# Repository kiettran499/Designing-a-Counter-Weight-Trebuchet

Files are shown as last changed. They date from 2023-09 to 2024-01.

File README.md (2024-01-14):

# Designing-a-Counter-Weight-Trebuchet

<p align="center">
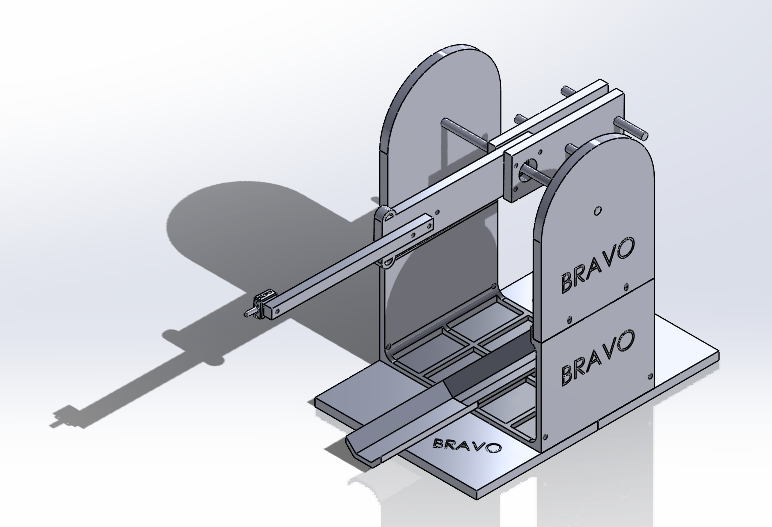
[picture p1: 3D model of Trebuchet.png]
  

## Description

- This project allows us to design and build the trebuchet which can throw the object like ping-pong ball over 5 meters using at least 2 500g PASCO weight.
- To design the trebuchet, there are several parameters might make a major contribution to the result and effectiveness of the trebuchet:
  - Mass Ratio between the Counterweight and the Projectile from law of conservation of energy.
  - Arm length ratio.
  - Friction in fulcrum.
- Some requirements:
  - The Trebuchet should not have more than 12 parts.
  - Each part should be able to fit into a 15 x 15 x 15 cm box.
  - The parts should have constant thicknesses of either 3 mm, 5 mm, or 10 mm and be made from Acrylic materials.
  - The Trebuchet shall permit aiming, which means it should be able to be adjusted for firing at different ranges and angles.

## Design & Result

- After doing calculations and simulate it in trebuchet virtual simulation, We came to the design.
<p align="center">
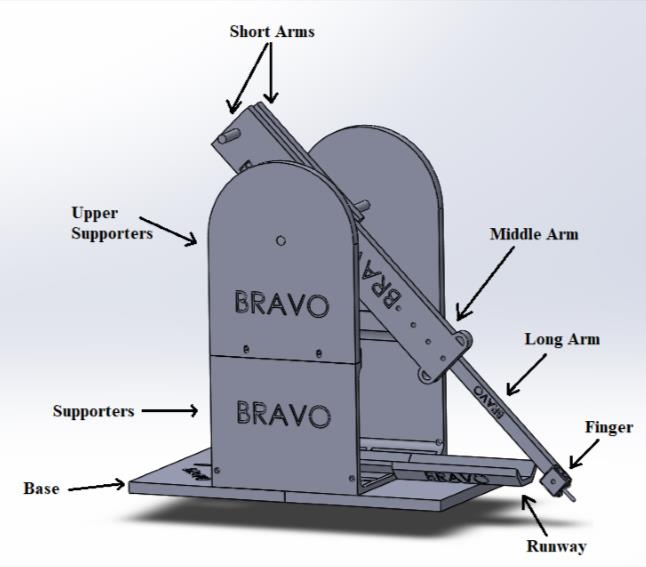
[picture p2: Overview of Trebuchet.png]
  
  
- Bill of Material.
<p align="center">
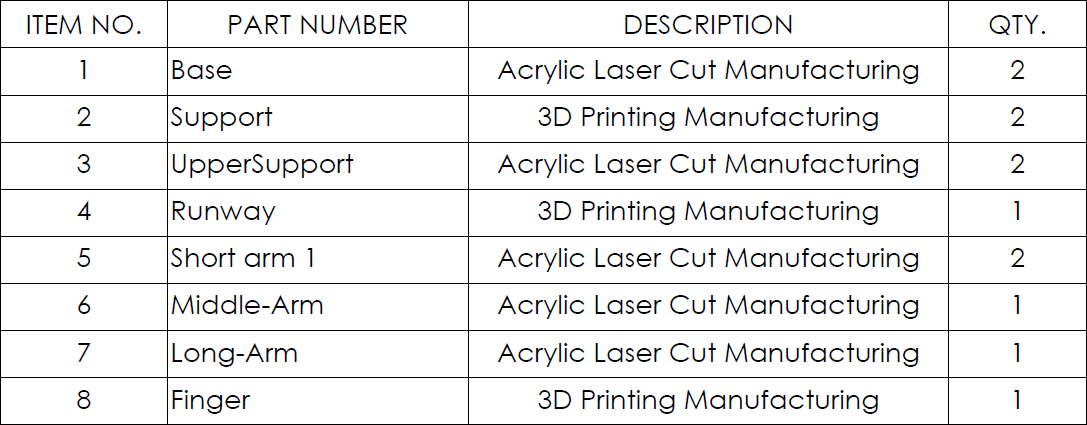
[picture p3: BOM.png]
  

- Exploded View of Trebuchet.
<p align="center">
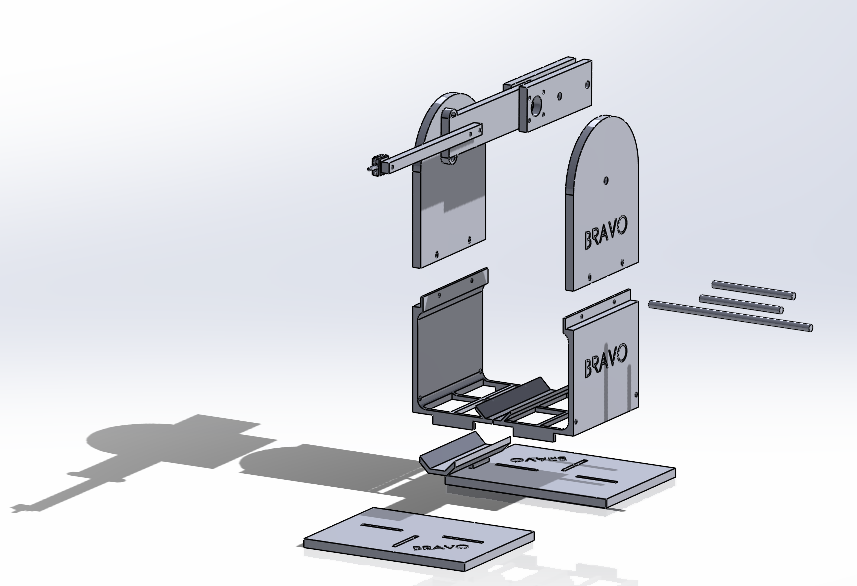
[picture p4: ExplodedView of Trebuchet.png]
  

- Exploded View of Trebuchet (Animation GIF).
<p align="center">
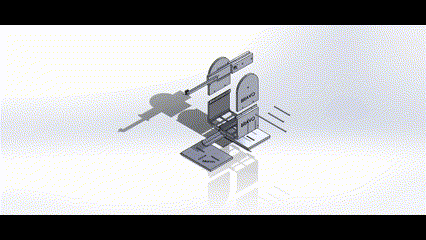
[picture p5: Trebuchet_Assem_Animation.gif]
  

- In conclusion, the trebuchet has 12 parts in total and each of them is fit into a 14 x 14 x 14 cm box. The projectile is the Ping-Pong ball and we choose 4 PASCO 500 grams weights whose total mass is 2000 grams.
- The length ratio between long and short arm is 4:1. The height of pivot is 23.5 cm as the height of each PASCO weight is 9cm and the short arm is 8cm, and we do not want them to hit the ground or the projectile runway when dropping. To leverage the arm ratio even more, we choose the sling whose length is close to that of the long arm, 30cm.
- Result: in the demonstration evaluation section, we had
  - 3 shots to test distance and all 3 shots are over 5 meters.
  - 1 shot to test accuracy and we had successfully hit the target at 4 meters.

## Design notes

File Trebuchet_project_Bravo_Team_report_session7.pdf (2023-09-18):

OENG1505 – Creative Engineering CAD | Page 1 of 21

# Class Project Designing a Counterweight Trebuchet

Student Numbers | Student Names:
s3758994 s3752562 s3741189 s3754450 s3757327 s3750474 | Nguyen Quoc Minh Truong Minh Phu Tran Anh Kiet Hoang Minh Quan Le Ngoc Duy Tran Vu Thao Uyen
Group | Bravo Team (session 7)
Lecturers: | Mr. Trung Nguyen Mr. Khoa Tran
Date: | 24-December-2020

Contents
1. Project Definition and Aim | 2

### 2. Design Theory and Methodology | 3

### 3. Design Mechanism and Calculations | 7

### 4. Device Description | 9

### 5. References | 17

### 6. Appendixes | 18

List of Figures

Figure 1. An overview of the trebuchet | 3
Figure 2. How trebuchet works | 7
Figure 3. How Ping-Pong ball can be slipped out the sling | 7
Figure 4. Projectile range in trebuchet virtual simulation | 9
Figure 5. Short arm of the trebuchet | 10
Figure 6. Middle arm of the trebuchet | 10
Figure 7. Long arm of the trebuchet | 11
Figure 8. Finger of the trebuchet | 11
Figure 10. Base of the trebuchet | 12
Figure 11. Lower support of the trebuchet | 13
Figure 12. Upper support of the trebuchet | 13
Figure 13. Runway for the trebuchet | 14
Figure 14. How to assemble the arm | 15
Figure 15. Completely assemble the arm | 15
Figure 16. How to assemble base and support towers | 16
Figure 17. Assembling Arm and Base-Support Towers | 16
Figure 18. Completely assemble trebuchet | 17

### 1. Project Definition and Aim

This project allows us to design and build the trebuchet which can throw the object like ping-pong ball

over 5 meters using at least 2 500g PASCO weight. We divide the trebuchet into 2 big parts (base tower

and arms) to easily to design and build. Since the requirement ask us to create the parts which

fit with limited dimension, we cut each big part into pieces that can meet the condition.

- Base Tower: Act like the foundation to hold firm for any movements of Arms.

It includes 3 small parts which are upper supporters, supporters and base.

- Upper Supporters: 2 pieces, they locate at the top of the base tower to hold the main

axis for the trebuchet. They are constructed by Laser Cutter.

- Supporters: Cut into 2 sides, which are same dimension and suitable with the

box, they connected with the upper supporters as well as base by joints,

then fixed by bolts and nuts. It locates underneath the supporters to maintain the

balance for the trebuchet. They are built by 3D print.

- Base: created by Laser Cutter and place at the bottom of the trebuchet and keep the

important task that make sure the trebuchet upright and does not lose

the equilibrium when it is operated.

- Runway: the place for the projectile to stand before the trebuchet activate, also

the road for it to run when the object starts working. It is produced by 3D Printer.

- Accounting for 7 out of 12 parts.
- Arms: the important part of the project which decide the throwing distance of the projectile.

It combines by finger, long arm, middle arm and short arm. The Arms are created by Laser

Cutter excepted Finger which is constructed by 3D Printer.

- Finger: to hold the sling of the projectile. The tool to control the release angle

when the trebuchet operated.

- Long arm: connector between the finger and the middle arm.
- Middle arm: to link the long arm with the main axis. Specially, the length of

the longarm can be adjusted by the joints which use to connect with the middle arm.

- Short arm: there are 2 short arms places at the end of the Arms, which are keeping

the middle arm at centre. They are big and thick enough for hooking at least 1kg of

mass.

- Accounting for 5 out of 12 parts.

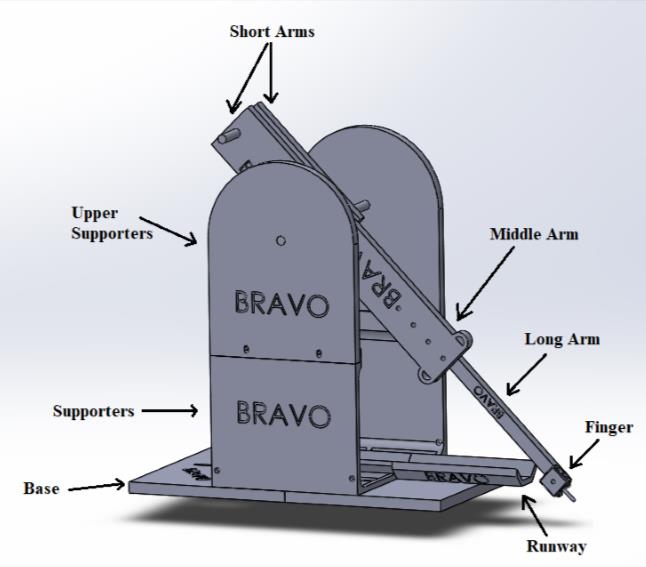
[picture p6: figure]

Figure 1. An overview of the trebuchet

### 2. Design Theory and Methodology

- Conservation Energy:

Basically, a trebuchet takes advantage of potential energy from a falling counterweight hanged at a

predefined height and transfer it into a moving projectile which is laid initially on the ground.

The transferred energy provides work to lift the projectile up against gravity force as well as initial

velocity for it. Thus, we can somehow determine the initial velocity of the projectile right at the time

it is about to launch.

On one side of the equation, we have the potential energy of the counterweight. Given its potential

energy at ground level is zero, gravitational potential energy of the counterweight is achieved by:

ECW = mCW × g × ∆hcw

Where mCW is the mass of the counterweight (kg), g is gravitational acceleration, ∆hcw is change is

in height of the counterweight when it is dropped at the lowest point and the projectile is about to

fire.

There are also additional operands, the increase in gravitational potential energy when the projectile

is being lifted and rotational kinetic energy when the arm is rotating. Our energy conservation formula

is eventually: mcw | × g | × | ∆hcw | =

1
2
mp | × | v
2 | + | mp | × g × ∆hp

Re-arrange the above formula, we have v = √
2 × [ (mcw×g × ∆hcw | ) − (mp×g×∆hp | ) ]

mp

(1)

From the formula (1), we can achieve a much greater initial velocity for the projectile by increasing

the mass and the distance dropped of the counterweight while decreasing the mass of the

projectile. The greater initial velocity will eventually ensure a larger firing range, based on projectile

motion analysis. [1]

- Project motion:

Since the projectile in this case is the Ping-Pong ball suffer Rotational Kinetic Energy when it starts to

leave the trebuchet and Gravitational Potential Energy when it falls down because of gravity. The ball

will move in the vertical and horizontal axis. The velocities of the projectile are vx = v × cos θ

and vy = v sin θ ( v is the magnitude of velocity, θ is its direction relative to the horizontal). [2]

In horizontal motion: [3]

v0x = vx, x = x0 + vx × t

In vertical motion:

y = y0 +

1
2

(vx + v0 )t

vy = vy,0 × g × t

y = (y0 + vy,0 × t) − (

1
2

× g × t

2
)

vy

2 = vy,0

2 − 2 × g × (y − y0)

Time of flight:

t =

2 × v0 × sinθ
g

Maximum height reached:

H =

2 × v0

2 × sin2θ
2 × g

Maximum Range:

R =

v0

2 × sin2θ
g

Where: v0 is the initial velocity (m/s).

Vx is the velocity (along the x-axis) (m/s).

Vy is the velocity (along the y-axis) (m/s).

sinθ is the component along the y-axis.

cosθ is the component along the x-axis.

g is the acceleration due to gravity (g = 9.8 m/s² ).

t is the time taken (s).

- Rotational Dynamic

Because the trebuchet works by using the potential energy from a falling counterweight hanged at a

predefined height to launch the projectile (Ping-Pong ball), it bears a certain amount of energy which

is called Rotational kinetic energy. The formula is

| | Kr | =
| | | 1
| | | 2 × I × ω2 [4]

Where:

ω (

radians

sec | ) is angular speed = | ∆θ ∆t
(∆θ is total covered. ∆t is total taken) [5]
I = | ∑ | mir

2
i | = | m1r

2
1 | + | m2r

2
I | 2 | + ⋯ | (m is the mass of the particle (kg), r is the distance from

the particle to the centre of rotation (m))

Because the arm of our trebuchet has a certain mass, the Moment of Inertia has additional equation:

I =

1
3

mL

2
(where m is the mass of arm (kg), L is the length of the arm(m)).
- Moments or Torques: [6]

From the trebuchet: taking the clockwise direction as being positive, the total moment acting on the

trebuchet:

τtotal = ∑τi

| | | n

i=1

= τCW − τprojectile

In general, if the angle between the direction of the force and the line towards the pivot point is theta,

θ, the equation for the moment of the force about the pivot point is:

τ = Fdsinθ

Where F is the magnitude of the force acting on the object, d is the distance from the pivot point to

where the force is acting, θ is the angle between the direction of the force and the line towards the

pivot point.

It has a massless beam as well. During the movement of the trebuchet, it will experience a torque due

to the unbalanced weights, which has a magnitude

τ = mCW.g.lSA. sinθ − mprojectile.g.lLAsinθ

= g. sinθ. (mCW.lSA − mprojectile.lLA).

Where:

mCW: mass of the counterweight (kg).

lSA: length of the short arm (m).

mprojectile: mass of the projectile (kg).

lLA: length of the long arm (m).

g: gravitational acceleration (m/s²
).

θ: the angle between the direction of the force and the line towards the pivot point.

- Affecting Factors: Several parameters might make a major contribution to the result and

effectiveness of the trebuchet:

- Mass Ratio between the Counterweight and the Projectile from law of conservation

of energy, it can be concluded that heavier counterweight results in greater

gravitational | potential | energy, | which | then | leads | to | much | kinetic

energy converted into the projectile. In addition, heavier counterweight leads to

more torque generated about the fulcrum.

- Arm length ratio: Because of the mass ratio between counterweight and projectile,
in | order | to | ensure | the | torque | applied on the long | arm | is | large

enough for the entire arm to rotate and angular acceleration of the projectile to

be also large, arm ratio should be taken into accounts as well.

- Friction in fulcrum: Obviously, friction in fulcrum can decrease the angular

acceleration of the projectile and thus affects its launching velocity. Therefore, we

decide to use a ball bearing for the rotational movement of the arm.

- Action Plan:
- Step 1: Determine all basic parameters related to arm lengths, pivot height, mass ratio

between counterweight and projectile to fulfill the requirement: firing a spherical

projectile whose diameter is up to 45 mm and weight 2.7 grams over at least 5

meters.

- Step 2: Determine appropriate specific dimensions for all parts of the trebuchet so

that not only do they accommodate the deliverable from step 1 but also each of

which is fit into a 14 x 14 x 14 cm box.

- | Step | 3: | From all | the parts | defined in | step | 2, we | will | decide how

each part is manufactured: which part will be lasers cut, which one will be 3D

printed. The parts in 3D will be carefully selected as only 4 parts are permitted.

### 3. Design Mechanism and Calculations

- Design Mechanism [7]

When the trigger holding the arm for trebuchet is released, the counterweight will fall down. During

that process, the Ping-Pong ball (projectile) will be dragged and slide on the runway by the sling. The

time when the Ping-Pong ball leaves the runway, it swings freely through an arc. At some point, the

Ping-Pong ball will be released out of the sling because the one end of the sling will be slipped out of

the finger (based on the angle between finger and long arm).

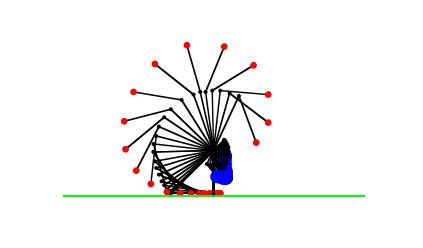
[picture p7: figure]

Figure 2. How trebuchet works

To be easier to understand how Ping-Pong ball slipped out of the string, it can be explained that the

sling just only exerts a tension along itself. Within the direction indicated, the rotating Ping-Pong ball

will exert a force on the one end of the sling, and it tends to pull the one end of the sling along a finger

until that one end of the sling is slipped out of the finger and at that time, the ping-pong ball will fly a

range.

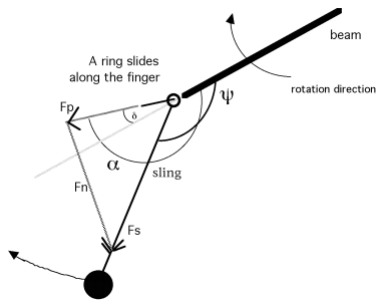
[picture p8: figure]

Figure 3. How Ping-Pong ball can be slipped out the sling

- Design Calculation

Following the action plan above, we first decided some parameters as constant for the sake of ease

of calculations since the trebuchet is a complex machine. In terms of mass ratio between the

counterweight and projectile, we ensure the mass of counterweight is as heavy as possible in relation

to that of the projectile. Thus, we choose 4 PASCO 500 grams weights whose total mass is 2000

grams. To hang 4 PASCO weights on the short arm, we have to hang them in parallel, which makes

short arm no shorter than 8 cm for the sake of durability. The length ratio between long and short arm

is 4:1. The height of pivot is 23.5 cm as the height of each PASCO weight is 9cm and the short arm is

8cm, and we do not want them to hit the ground or the projectile runway when dropping. To leverage

the arm ratio even more, we choose the sling whose length is close to that of the long arm, 30cm. With

all these constants and based on the conservation energy formula discussed above, the initial velocity

of the projectile is (assuming the long arm is nearly vertical and releasing angle is 45 degree):

V = √
2(mcw × g × ∆hcw − mp × g × hp) mp

= √
2×(2×9.8×0.1465 −0.0027 ×9.8 ×0.7813) 0.0027

= 45. 95 (m/s)

The range then can be partly determined by applying the projectile motion formula, assuming the

projectile released at 45 degree:

R =

v

2
0Sin2θ
g

= 215.45 (m)

Obviously, the actual result is far smaller than the calculated one as there are several factors such

as air resistance, friction in fulcrum that might affects the range of firing projectile. In addition, the

range is calculated given that all of potential energy generated from the counterweight is ideally

transferred into kinetic energy of the projectile completely while in real life, this situation is hard to

achieved. To test our assumption, due to difficulty in real life manufacturing at the first stage of this

project, we rely on a virtual trebuchet simulation to examine our parameters:

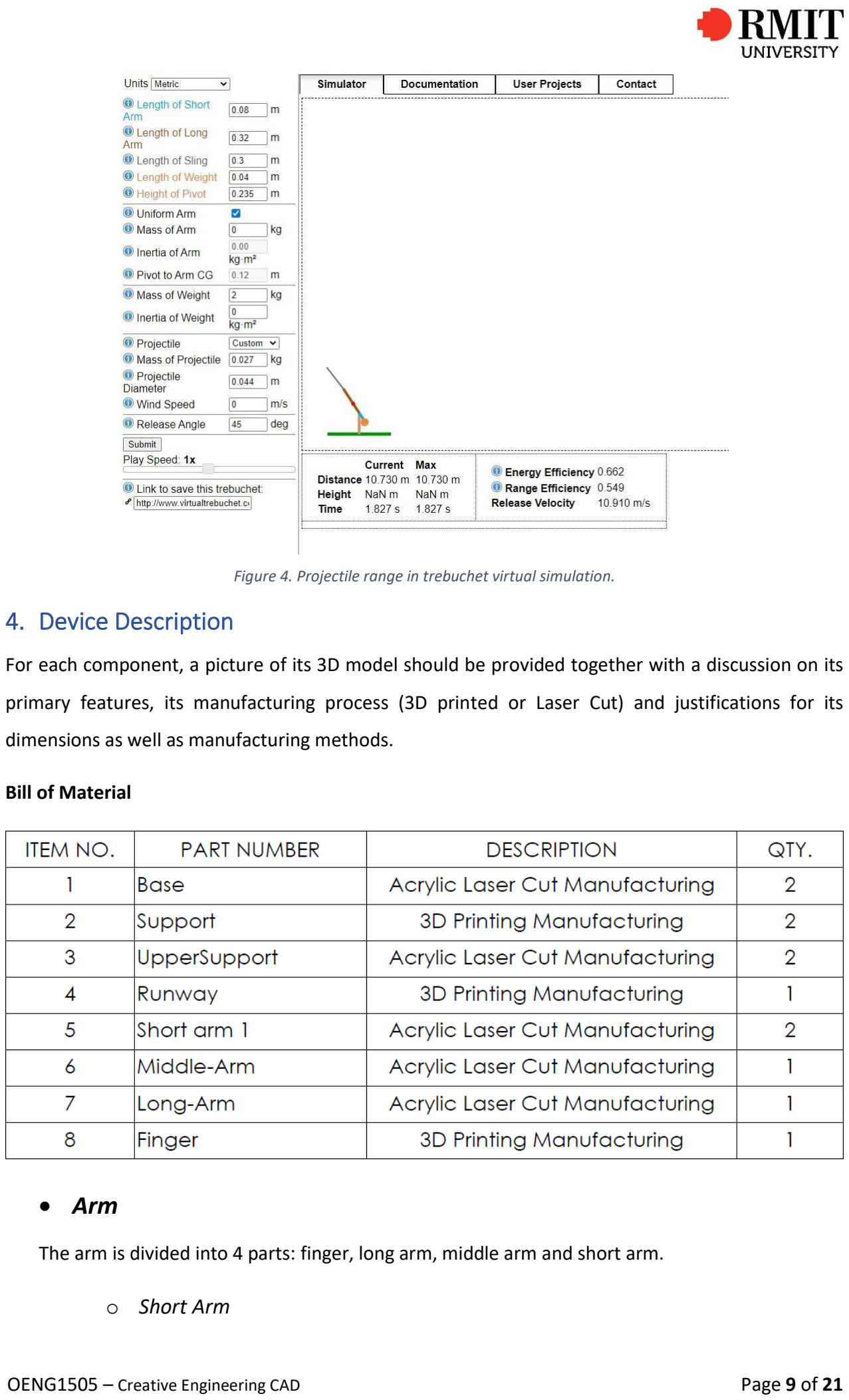
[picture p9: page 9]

Figure 4. Projectile range in trebuchet virtual simulation.

### 4. Device Description

For each component, a picture of its 3D model should be provided together with a discussion on its

primary features, its manufacturing process (3D printed or Laser Cut) and justifications for its

dimensions as well as manufacturing methods.

Bill of Material

### - Arm

The arm is divided into 4 parts: finger, long arm, middle arm and short arm.

- Short Arm

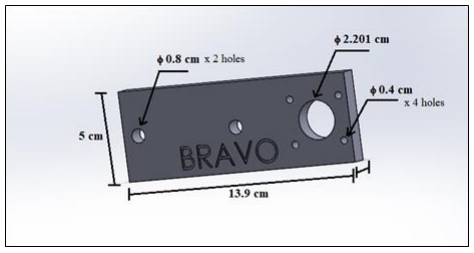
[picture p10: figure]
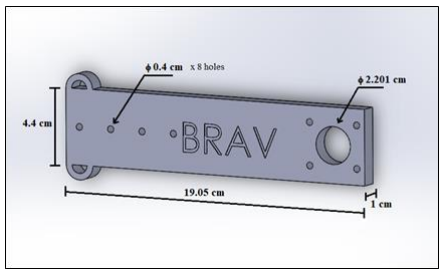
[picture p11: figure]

OENG1505 – Creative Engineering CAD | Page 10 of
21

Figure 5. Short arm of the trebuchet

The short arm is connected to the middle arm at one end and the counterweights, which will be the

PASCO 500g weight at the other. The short arm also has a hole with the diameter of 22 millimeter to

fit the ball bearing. At the end, which is used to connect the counterweights, there are two holes.

These holes are there to put a metal beam through and hang the counterweights on that beam. There

are two holes to support multiple blocks. The short arm will be manufactured by the laser cutter. It

has a bounding box dimension of 13.9cm x 5cm x 1cm, which fits the dimension requirement for laser

cut parts. The specific dimensions will be shown in the appendix section bellow.
- Middle Arm

Figure 6. Middle arm of the trebuchet

The middle arm is connected to the long arm at one end and the short arm at the other. They are

connected by using nuts and bolts, which are put through holes with the diameter of 4 millimeter. At

the end, which is connected to the short arm, there is a big hole with the diameter of 2.2 centimeters,

which will be used to put a ball bearing in. The ball bearing is there to eliminate most of the friction.

At the end, which is connected to the long arm, there are 4 holes, which will be used to control the

total length of the arm. At the other end, there are two holes in the shape of an arc, which is used to

connect the middle arm to the trigger. The middle arm will be manufactured using the laser cutter. It

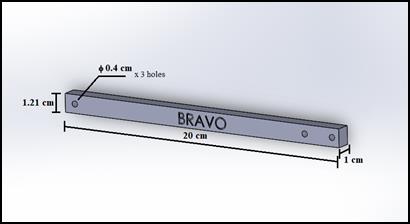
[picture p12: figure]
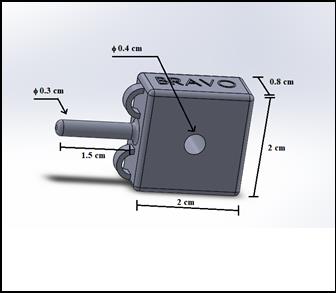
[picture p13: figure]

OENG1505 – Creative Engineering CAD | Page 11 of

has a bounding box dimension of 19.05cm x 6.1cm x 1cm, which fits the dimension requirement for

laser cut parts. The specific dimensions will be shown in the appendix section bellow.
- Long Arm

Figure 7. Long arm of the trebuchet

The long arm is connected to the finger at one end, and the middle arm at the other. They are

connected with nuts and bolts, which will be put through the holes on the body of the long arm. These

holes have the same diameter of 4 millimeter.

The long arm will be manufactured by the laser cutter. It has a bounding box dimension of 20cm

x 1.21cm x 1cm, which fits the dimension requirement for laser cut parts. The specific dimensions will

be shown in the appendix section bellow.
- Finger

Figure 8. Finger of the trebuchet

The finger is the most important part of the release mechanism of the trebuchet. It is connected to

the end of the long arm, via a nut and bolt with a diameter of 4 millimetres. The finger will be 3D

printed with tough resin. It has a bounding box dimension of 3.5cm x 2 cm x 1cm, which fits the

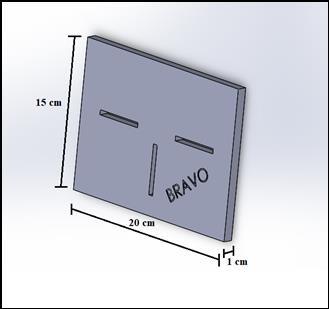
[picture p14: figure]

OENG1505 – Creative Engineering CAD | Page 12 of

requirements for 3D printed parts. The specific dimensions will be shown in the appendix section

bellow.

### - Tower

The tower is divided into 4 parts: base (front - rear), support (left - right), upper support (left - right)

and runway.

- Base

Figure 9. Base of the trebuchet

The base is the bottom foundation that is used to connect the support and later the whole

trebuchet. There are two pieces of the base, which are connected at the longer edge (the 20cm

edge) of each other. On the top of the base, there are 3 rectangular slots that cut through the base.

These slots are there so that the support and the runway, which will be discussed later in the report,

can be connected to via the tabs on those parts. The base will be manufactured by the laser cutter. It

has a bounding box dimension of 20cm x 15cm x 1cm, which fits the dimension requirement for laser

cut parts. The specific dimensions will be shown in the appendix section bellow.
- Lower Support

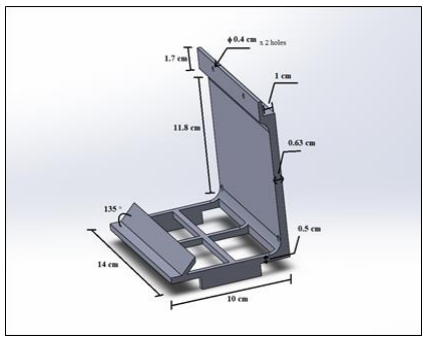
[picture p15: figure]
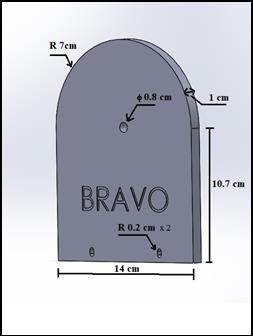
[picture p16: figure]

OENG1505 – Creative Engineering CAD | Page 13 of

Figure 10. Lower support of the trebuchet

The support is the part that is connected to the base at the bottom, and the upper support on top. It

has a distinctive "L" shape. At the bottom, there are two tabs, which are used to connect to the slots

on the base. Along with that, the support has one half of the primary runway. There are two holes,

with a diameter of 4 millimeters each to connect the support to the upper support via a nut and bolt.

The top of the support also has a "L" shape to let the bottom of the top support settle on. The bottom

of the support must have rectangular holes to reduce its volume and comply with

the volume restriction for 3D printed parts. There will be another support, which is mirrored along

the longer edge (the 14cm edge) of the part to complete the entire support. The illustration of this

will be shown in the assembly section later in the report. The support will be manufactured by the 3D

printer. It has a bounding box dimension of 14cm x 10cm x 1cm, which fits the dimension requirement

for laser cut parts. The specific dimensions will be shown in the appendix section bellow.
- Upper Support

Figure 11. Upper support of the trebuchet

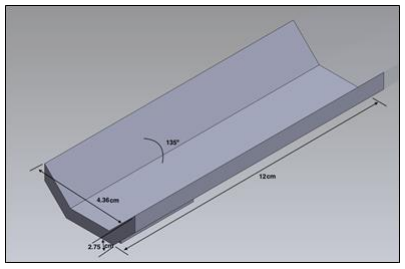
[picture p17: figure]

OENG1505 – Creative Engineering CAD | Page 14 of

The upper support is the part that is connected to the support and the connector beams, which is

connected to the arm. The lower half of the top support has a rectangular shape, while the upper half

of it is filleted with an arc which has a radius of 7 centimeters. At the center of the filleted arc, there

is a hole to put the connector beam through, which has a diameter of 0.8 centimeters. At the bottom

of the upper support there are two holes, with a diameter of 0.4 centimeters each, to connect the

upper support to the support using nuts and bolts.

The upper support will be manufactured by the laser cutter. It has a bounding box dimension of 14cm

x 17.7cm x 1cm, which fits the dimension requirement for laser cut parts. The specific dimensions will

be shown in the appendix section bellow.
- Runway

Figure 12. Runway for the trebuchet

This can be called the secondary runway, as the primary runway is integrated into the support. The

primary runway extends the total distance of the runway. The purpose of the runway is to control the

movement of the projectile. Initially, the projectile will be located at the end of the runway. When the

arm starts swinging, the projectile will follow the runway in a straight direction, minimizing

any disturbance to maximize the efficiency.

The runway has a "V" shape which was extruded to be longer. At the bottom of this runway, there is

a tab, which will be used to connect to the slot on the base. It was designed in a way that will fit the

projectile and will not be hit by the counterweights at the bottom most position.

The upper support will be manufactured by the 3D printer. It has a bounding box dimension of 12cm

x 4.36cm x 2.75cm, which fits the dimension requirement for 3D printed parts. The specific dimensions

will be shown in the appendix section bellow.

### - How to assemble all components

- Assemble all components for the arm

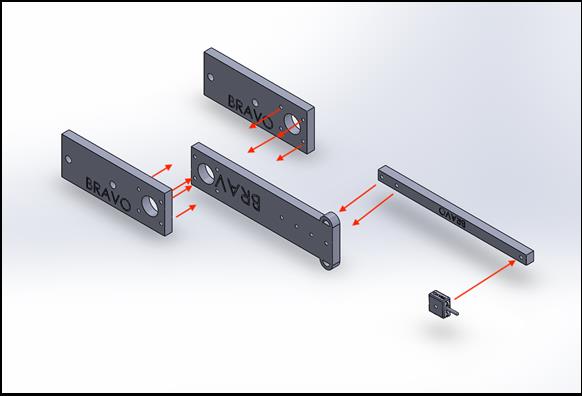
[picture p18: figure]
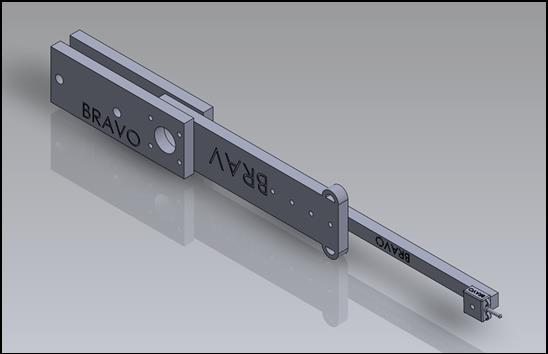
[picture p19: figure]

OENG1505 – Creative Engineering CAD | Page 15 of

Figure 13. How to assemble the arm

As mentioned above, the parts will be connected using nuts and bolts. Firstly, two short arms are

connected to the two sides of the middle arm. The four 4mm holes on the short arms need to be

aligned with those on the middle arm. Four long nuts are put through the holes and secured by four

bolts. Then, based on the chosen length of the entire arm, two holes of the long arm will be aligned

to the corresponding holes on the middle arm. And two nuts will be put through the two holes and be

secured with two nuts. Finally, the finger will be connected to the other end of the long arm. In a way

so that the finger is straightly aligned with the middle arm. The hole on the finger must be aligned with

that on the long arm. A nut will be put through the hole and be secured by a nut.

Figure 14. Completely assemble the arm

- Assemble all components for the base-support tower

First, the two bases and supports need to be aligned as shown in the figure. The tab at the bottom

of the runway is connected to the vertical slot on the rear base. Two upper supports will be connected

and aligned to the supports as shown in the figure. Four nuts will be put through the holes and be

secured with four bolts. Four tabs of the two supports will now be connected to the remaining four

horizontal slots on the base. Completely assemble the base-tower support

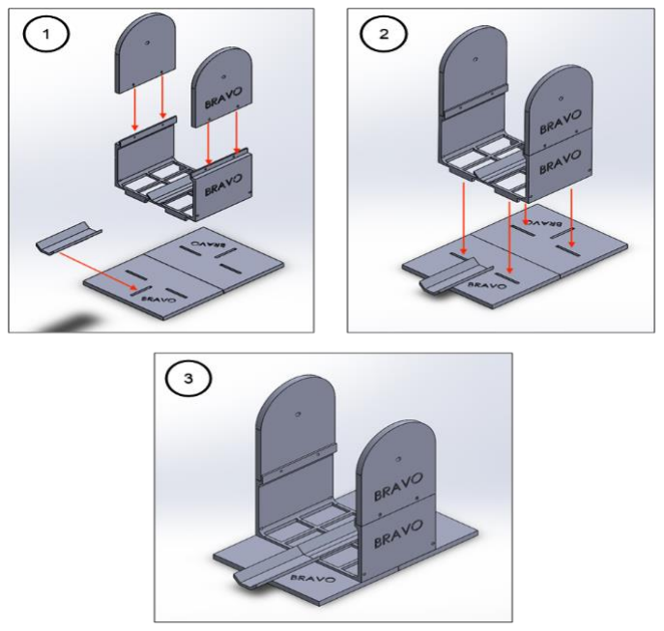
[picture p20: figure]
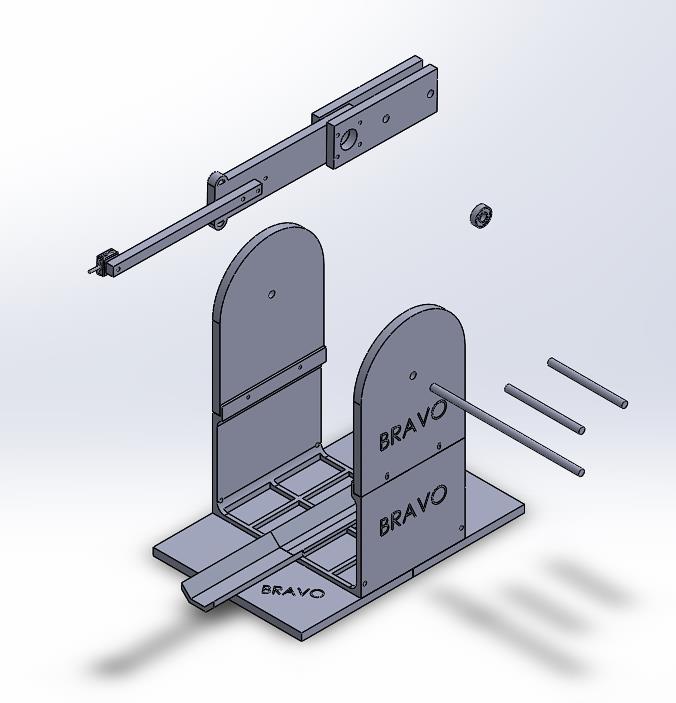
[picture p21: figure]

OENG1505 – Creative Engineering CAD | Page 16 of

Figure 15. How to assemble base and support towers

- Completely assemble trebuchet by assembling Arm and Base-Support Towers

Figure 16. Assembling Arm and Base-Support Towers

For assembling the arm and the base-support towers, our group used several connecting parts

including 1 Ball Bearing (with the parameter 8mm), 1 Connector Beams (with the diameter 8mm with

length 200mm), 2 Mass Beams (with the diameter 8mm and the length 100mm). Our group inserts

the Ball Bearing into the connection point between Short-Arm, Long-Arm and Middle-Arm of the Arm.

The main reason to use Ball Bearing to reduce friction to maximize efficiency of the system. After that,

we use the Connector Beam to insert through the Ball Bearing that already inserted into the

connection point of the arm. Finally, we connect 2 Mass Beams at 2 connection points at the end of

the Short-Arm.

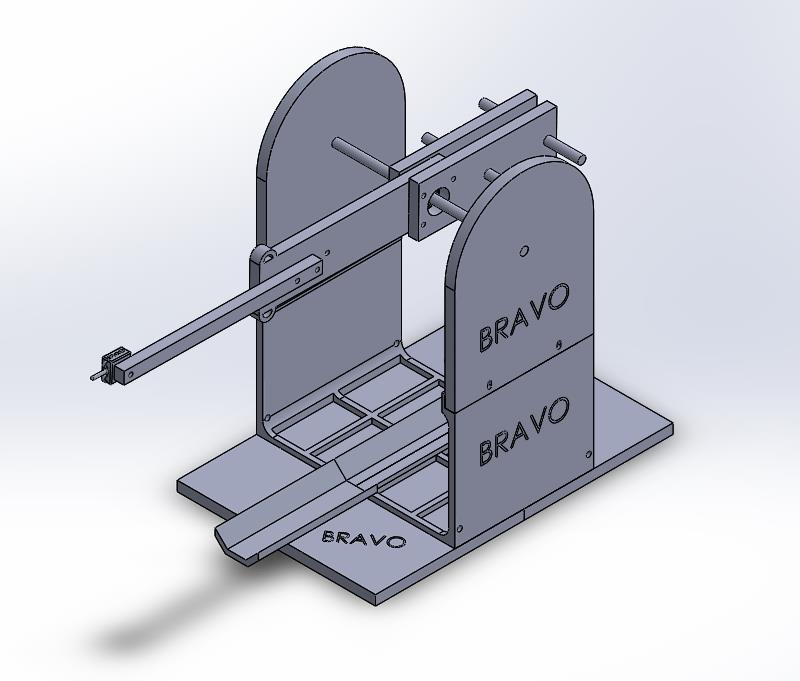
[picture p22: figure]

OENG1505 – Creative Engineering CAD | Page 17 of

Figure 17. Completely assemble trebuchet

### 5. References

[1] S. Lucas and S. Horners, "What affects the range of a trebuchet?", Ucl.ac.uk, 2020. [Online].
Available: | https://www.ucl.ac.uk/~zcapf71/Trebuchet%20coursework%20for%20website.pdf.
[Accessed: 09- Dec- 2020].
[2] "4.3 Projectile Motion - University Physics Volume 1 | OpenStax", Openstax.org, 2020. [Online].
Available: | https://openstax.org/books/university-physics-volume-1/pages/4-3-projectile-
motion#:~:text=h%3Dv20y,component%20of%20the%20initial%20velocity.&text=A%20rock%20is%2 0thrown%20horizontally,velocity%20of%2015.0%20m%2Fs. (https://openstax.org/books/university-physics-volume-1/pages/4-3-projectile-motion) [Accessed: 15- Dec- 2020].
[3] "GDPR", Byjus.com, 2020. [Online]. Available: https://byjus.com/projectile-motion-formula/. [Accessed: 11- Dec- 2020].
[4] | "Angular | Speed | Formula", Softschools.com, | 2020. | [Online]. | Available:
https://www.softschools.com/formulas/physics/angular_speed_formula/27/. [Accessed: 07- Dec-2020].
[5] | "Rotational | Energy | and | Inertia", Softschools.com, | 2020. | [Online]. | Available:
https://www.softschools.com/notes/ap_physics/rotational_energy_and_inertia/. [Accessed: 12-Dec- 2020].
[6] | "Isaac | Physics", Isaac | Physics, | 2020. | [Online]. | Available:
https://isaacphysics.org/concepts/cp_moments. [Accessed: 12- Dec- 2020].
[7] | D.B.Siano, Algobeautytreb.com, | 2020. | [Online]. | Available:
http://www.algobeautytreb.com/trebmath356.pdf. [Accessed: 06- Dec- 2020].

### 6. Appendixes for 2D-Drawings

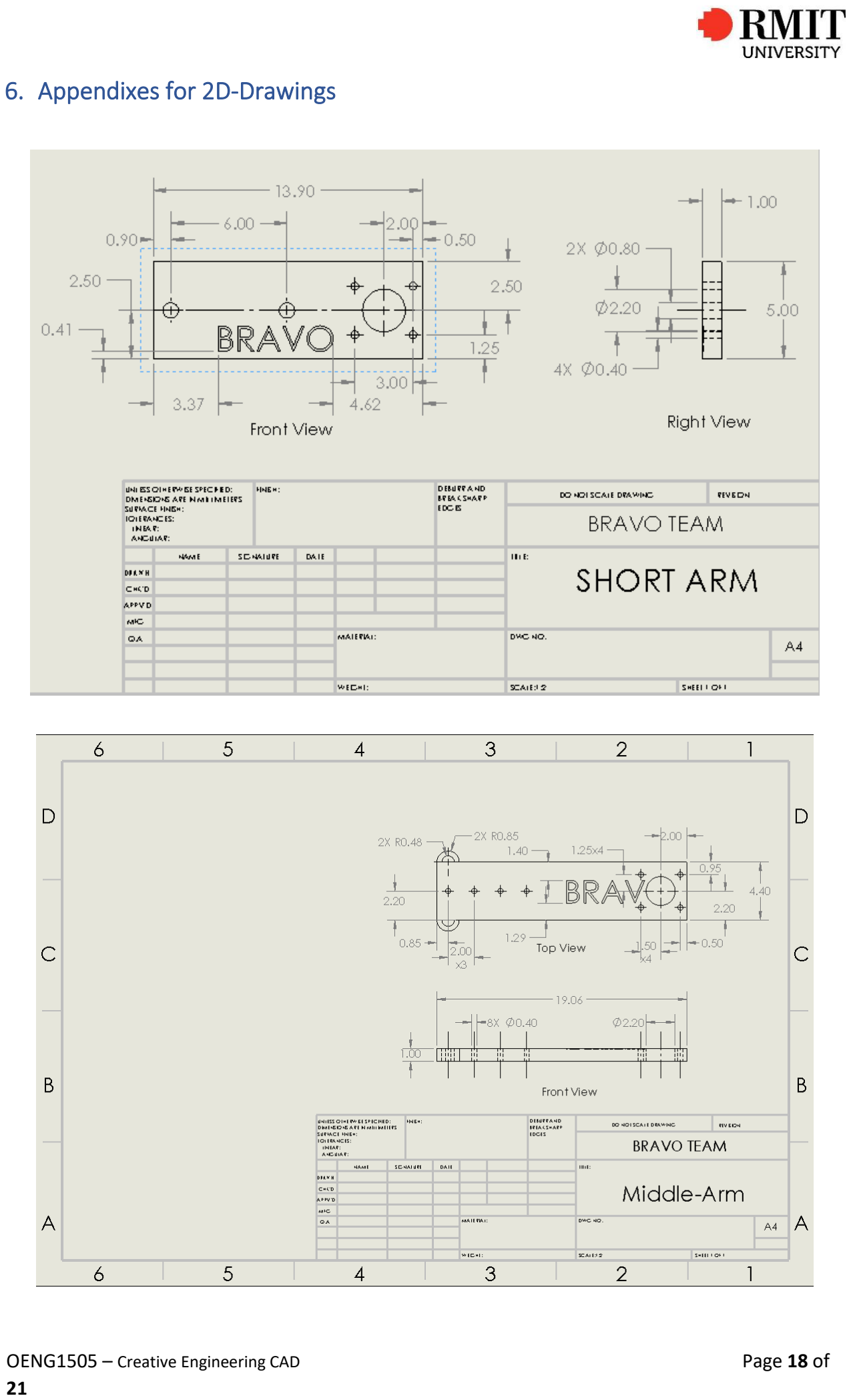
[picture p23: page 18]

OENG1505 – Creative Engineering CAD | Page 18 of

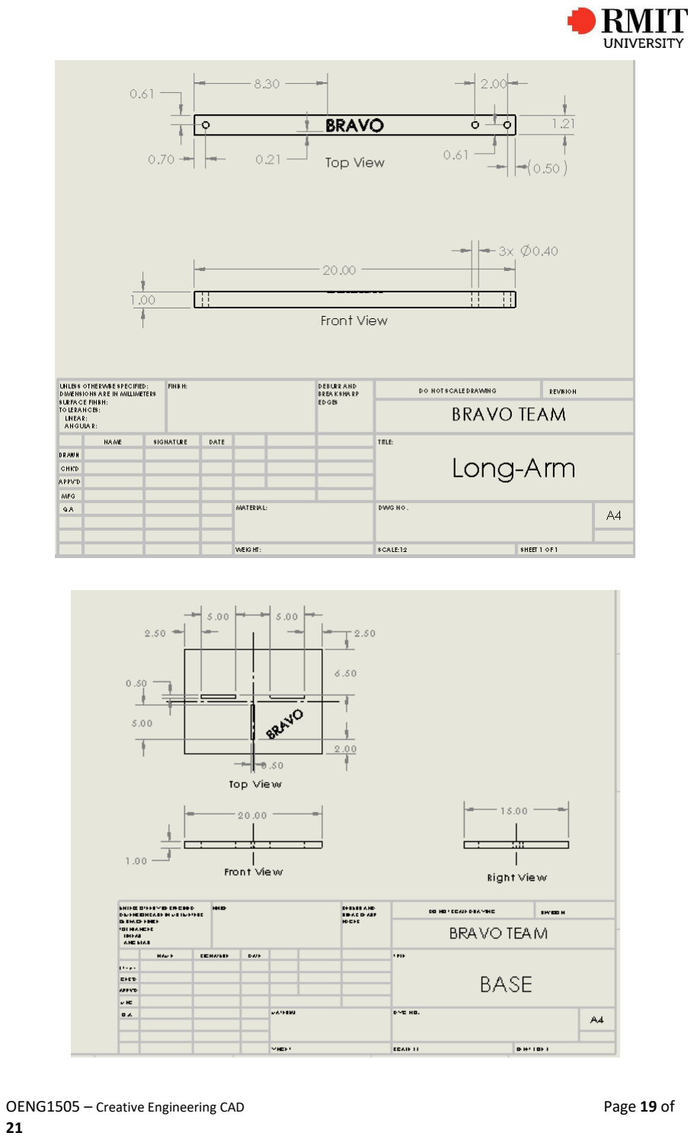
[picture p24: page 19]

OENG1505

– Creative Engineering CAD | Page 19 of

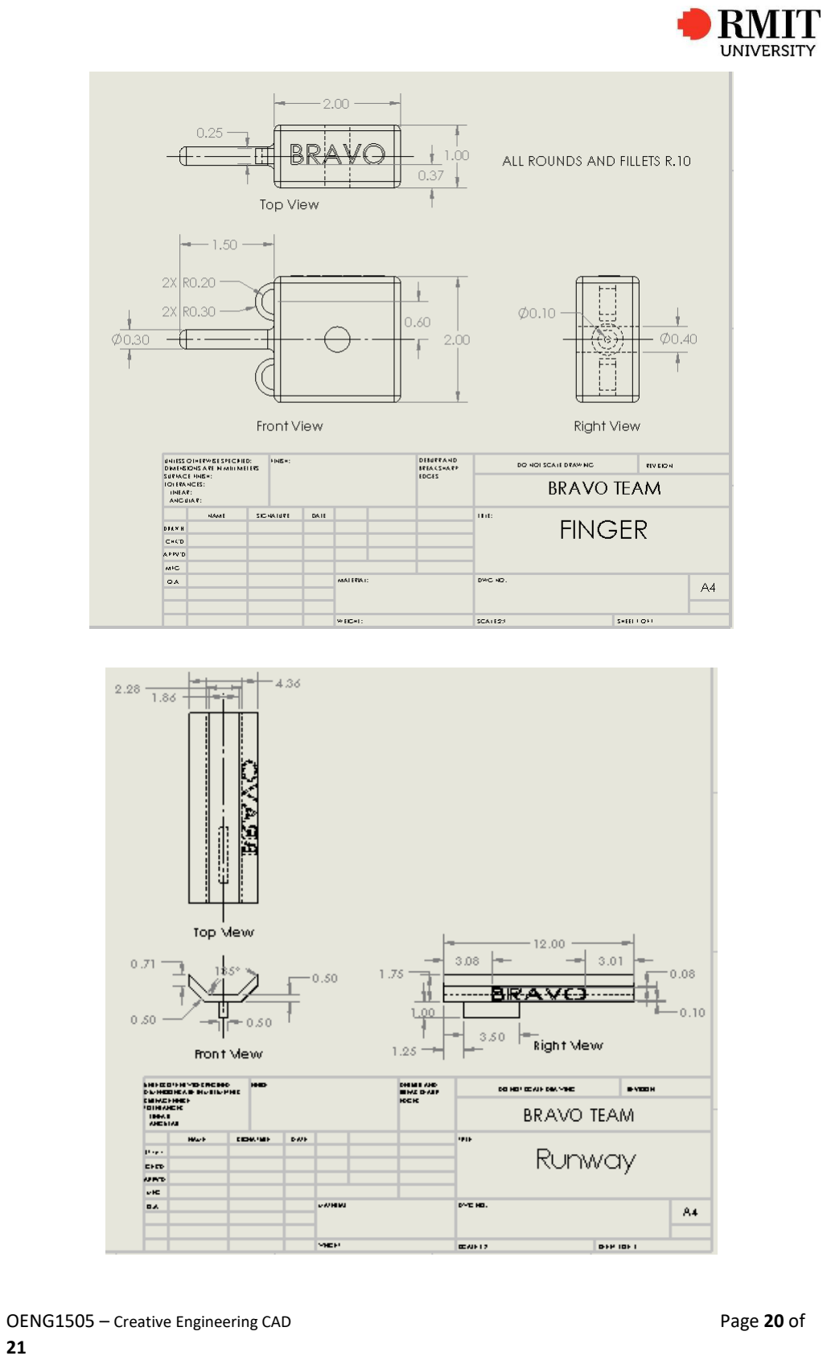
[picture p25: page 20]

OENG1505

– Creative Engineering CAD | Page 20 of

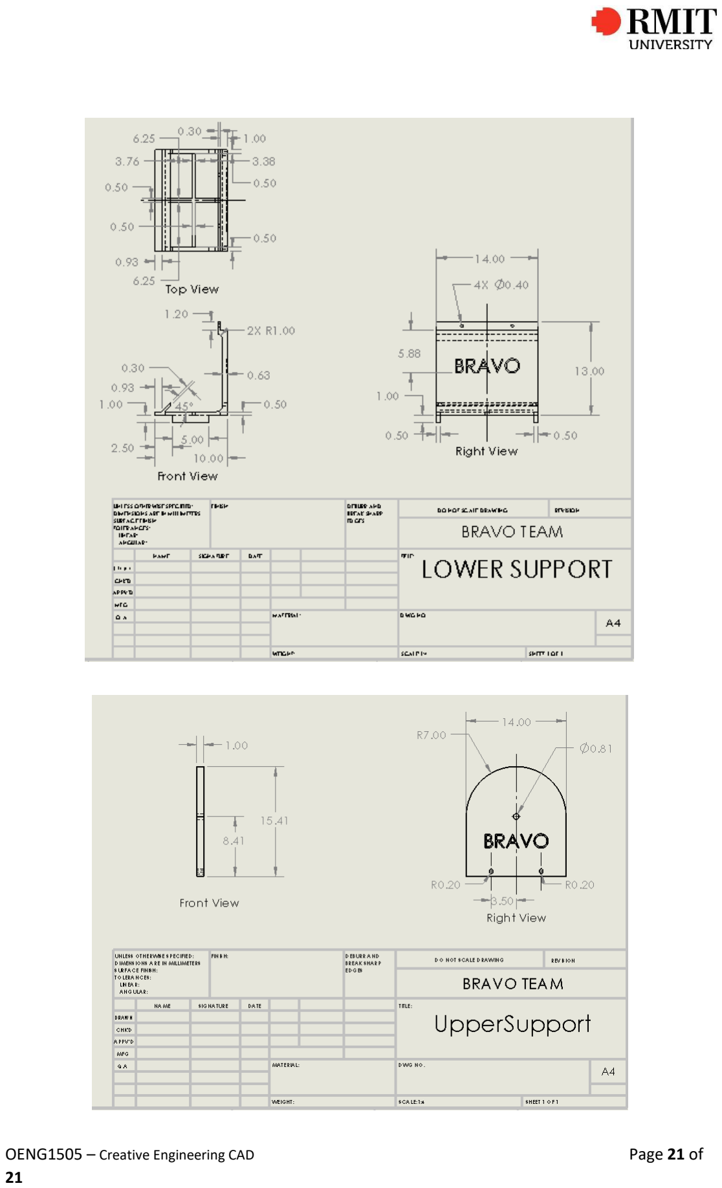
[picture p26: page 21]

OENG1505

– Creative Engineering CAD | Page 21 of

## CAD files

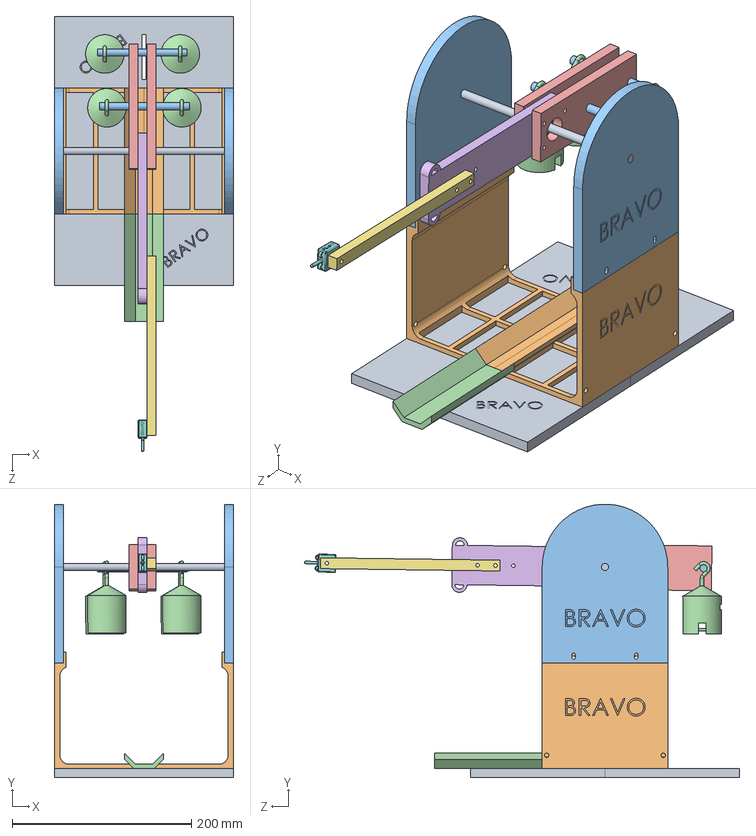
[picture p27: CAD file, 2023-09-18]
Trebuchet with Mass.SLDASM
200.0 x 304.9 x 485.1 mm
Base x 2
Support x 2
UpperSupport x 2
Runway
Short arm 1 x 2
Middle-Arm
Long-Arm
Finger
ConnectorBeam
BallBearing
MassBeam x 2
PASCO 500g Hooked Mass x 4

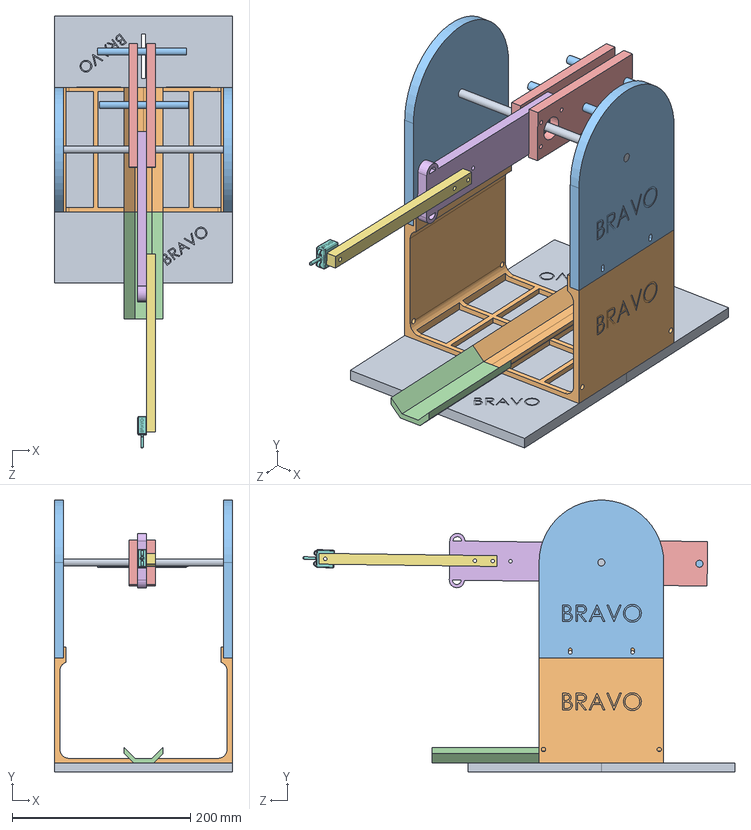
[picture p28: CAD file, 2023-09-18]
Trebuchet.SLDASM
200.0 x 304.9 x 485.1 mm
Base x 2
Support x 2
UpperSupport x 2
Runway
Short arm 1 x 2
Middle-Arm
Long-Arm
Finger
ConnectorBeam
BallBearing
MassBeam x 2
